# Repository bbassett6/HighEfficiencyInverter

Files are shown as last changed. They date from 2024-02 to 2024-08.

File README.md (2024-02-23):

Project Executive Summary

What is the design problem and why it should be solved?

With the growing popularity of student-led solar car racing competitions, newly established teams can have restrictive levels of funding to start their engineering endeavors. One of the most critical components of the competitiveness of their cars is the powertrain efficiency, which is heavily influenced by the quality and versatility of their motor controller. As of today, there are only two competitive options that are adopted by most teams, and both represent a substantial amount of the vehicle's cost (over a third of the electrical system's, approximately). This creates a tall barrier of entry for developing engineers to be exposed to real-life design environments that could deeply affect their career choices and subsequent impact in the world, which is why an open-source, accessible inverter would be impactful in the field of sustainable energy, and potentially many others.

What are the technical problems?

Technical problems include
•	Obtaining efficiency range values comparable or superior to present competitors’ while offering a substantially reduced price: 
Because of the size of the market, no substantial innovation has been made in mainstream options for approximately 14 years. Recent developments in SiC and GaN-based semiconductors could contribute a significant advantage compared to these outdated designs, but hitting required performance levels for a large range of possible motor and voltage configurations will be a challenge. Additionally, new control methodologies might be more applicable nowadays because of both device development and advances in control theory.
•	Maximizing efficiency while keeping the inverter design as tolerant as possible to high-voltage design changes depending on the application: 
Teams' choices of power per motor and DC bus voltage can vary drastically depending on the competition segment (multi- or single-occupant vehicles), creating a challenging optimization problem when attempting to make a product as efficient as possible for as many configurations as expected.
•	Minimizing inverter-driven high voltage system requirements: 
In addition to the DC bus compatibility, motor and motor sensing versatility is a factor that influences how seamless the product's integration can be, facilitating its adoption and potentially expanding its impact.
•	Power density (gravimetric, volumetric):
Being heavily influenced by the switching speed of the semiconductor devices being employed, recent product releases could be incredibly important to meet performance levels such as the DOE's 2025 Vehicle Technology goals.

What is the overall design/technical/objective(s)?

Design a financially (under US$ 1000) and technically accessible, high efficiency inverter for use in solar vehicle applications. The design should be easily replicable, testable, and employed by high-school level students. The final efficiency characteristics for applicable performance ranges (e.g. torque, speed, temperature), should be compatible with or surpass those of available options (WaveSculptor22, Mitsuba).

What is the proof of concept? What demonstrates that the solution works?

The proof of concept for the project could consist of a custom-made PCB for the selected power stage topology, containing components such as the switching devices, gate drivers, & high-voltage sensors. This would be complemented with an off-the-shelf development board containing the selected microcontroller and required peripherals, allowing full validation and operation of the converter without a finalized case and custom logic-stage PCB. Should this implementation work as expected, the project would move forward to unification and/or further customization of the boards to achieve a final unified package that is easily integrable.

Demonstrating the solution may involve attaching either an inductive load or a real motor to the inverter and measuring power losses through the power stage at various operating points (steady state cruising, acceleration, regenerative braking).

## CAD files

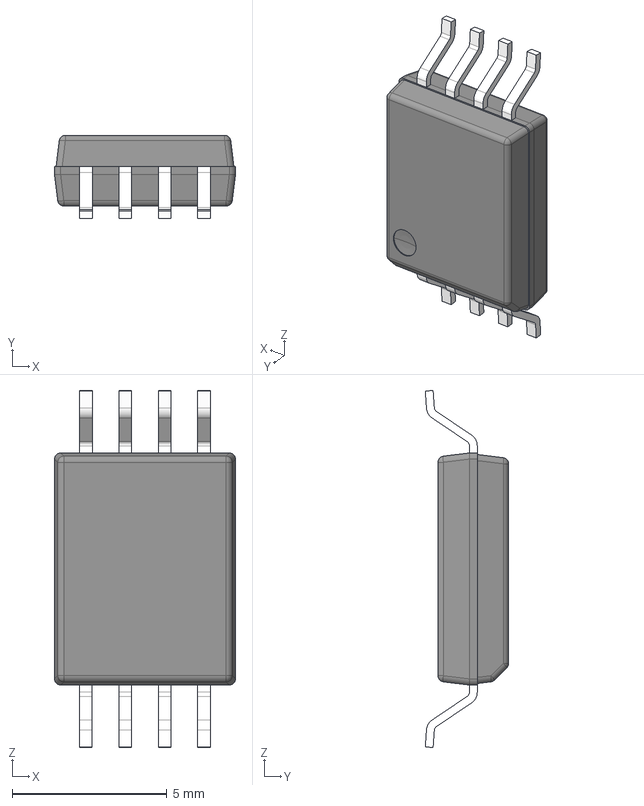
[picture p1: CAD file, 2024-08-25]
HEI_Power_Stage/Parts/AMC1311_KiCad/3D/AMC1311DWVR.stp
5.85 x 2.70 x 11.5 mm
BODY-SOIC
LEAD-DWV0008A x 8

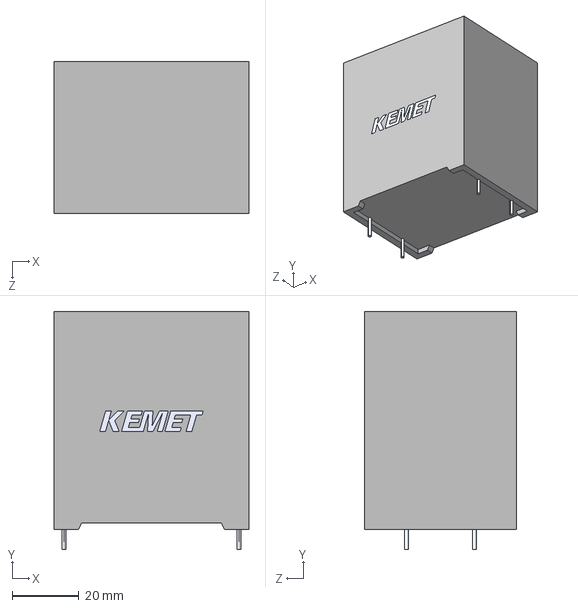
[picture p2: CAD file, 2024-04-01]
HEI_Power_Stage/Parts/C4AQ/C4AQLEW6210A3BK.stp
58.3 x 71.3 x 45.5 mm

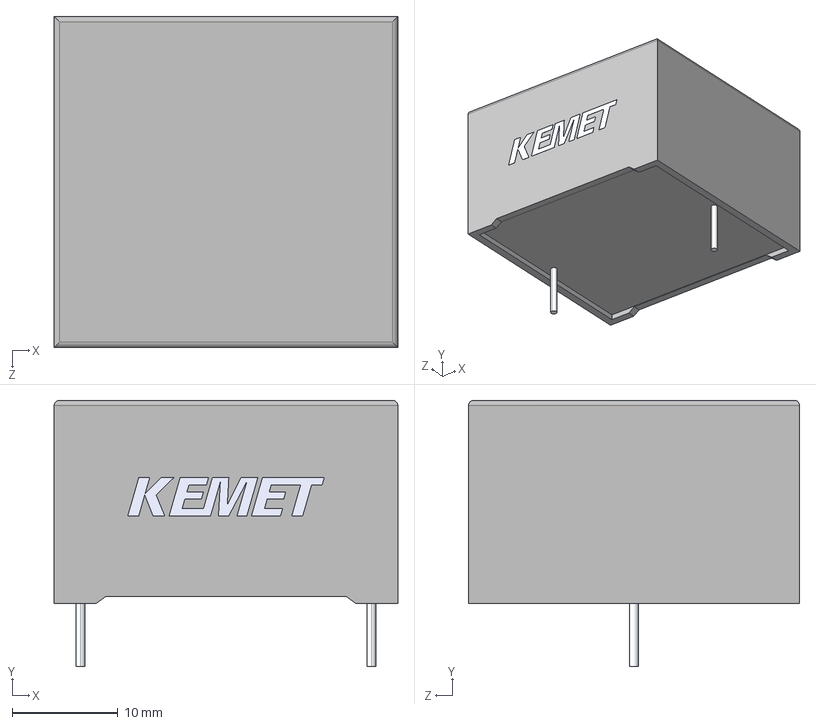
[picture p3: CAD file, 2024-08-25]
HEI_Power_Stage/Parts/C4AQLLU5150A19K _KiCad/3D/C4AQLLU5150A19K.stp
32.5 x 25.2 x 31.3 mm

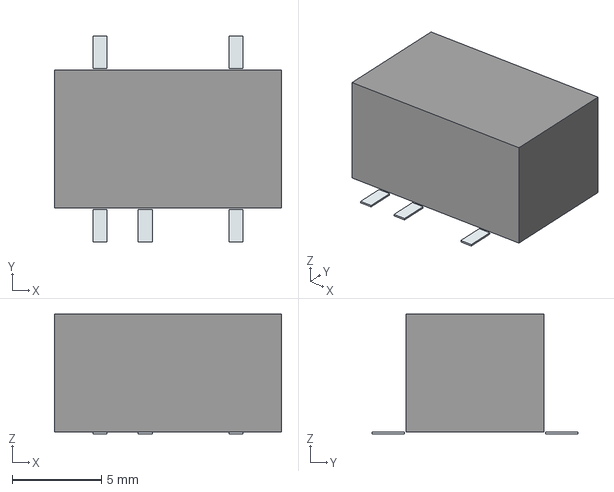
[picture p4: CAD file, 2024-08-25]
HEI_Power_Stage/Parts/CRE1S0505MC_KiCad/3D/CRE1S0505MC.stp
12.7 x 11.5 x 6.70 mm
Pins

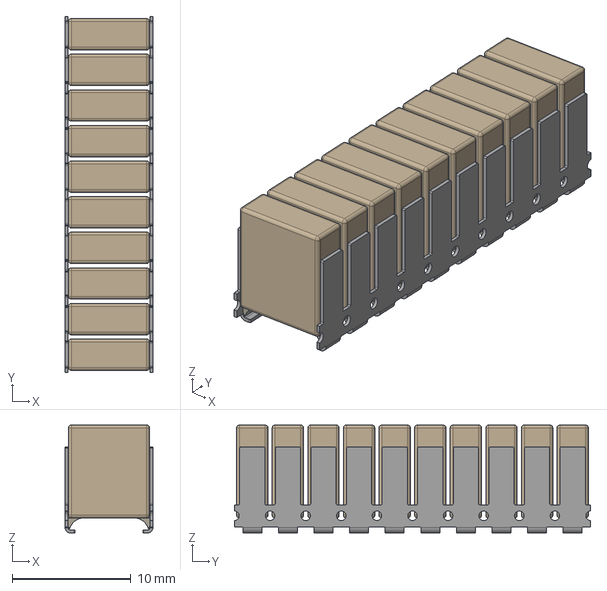
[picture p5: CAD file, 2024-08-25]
HEI_Power_Stage/Parts/B58035U5106M001_KiCad/3D/B58035U5106M001.stp
7.40 x 30.0 x 9.10 mm

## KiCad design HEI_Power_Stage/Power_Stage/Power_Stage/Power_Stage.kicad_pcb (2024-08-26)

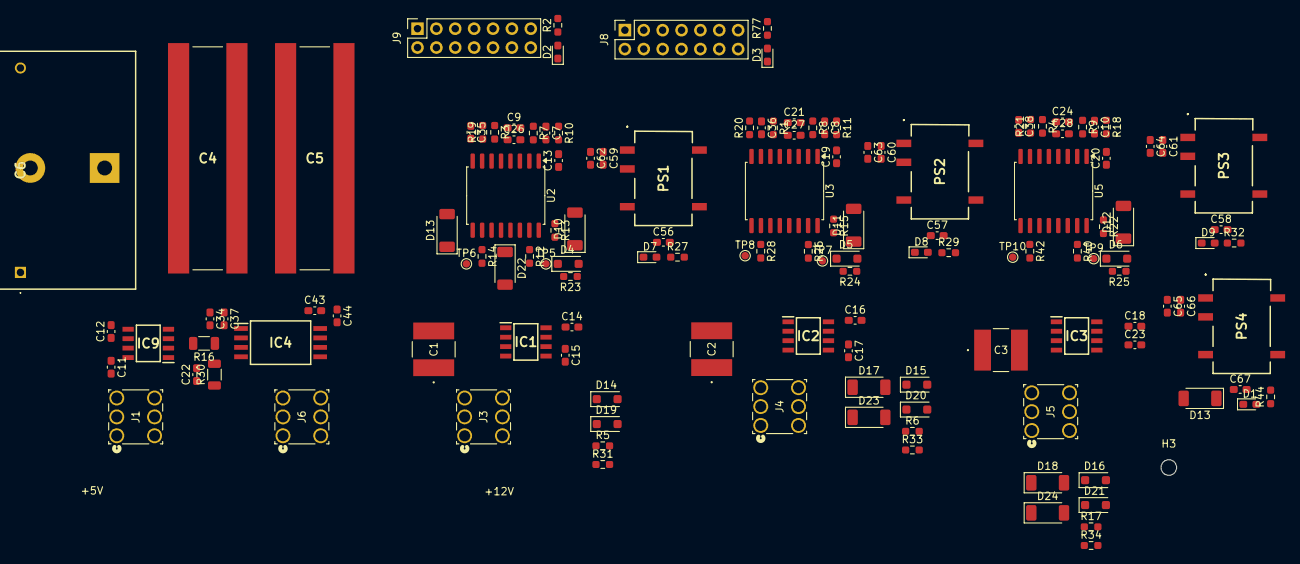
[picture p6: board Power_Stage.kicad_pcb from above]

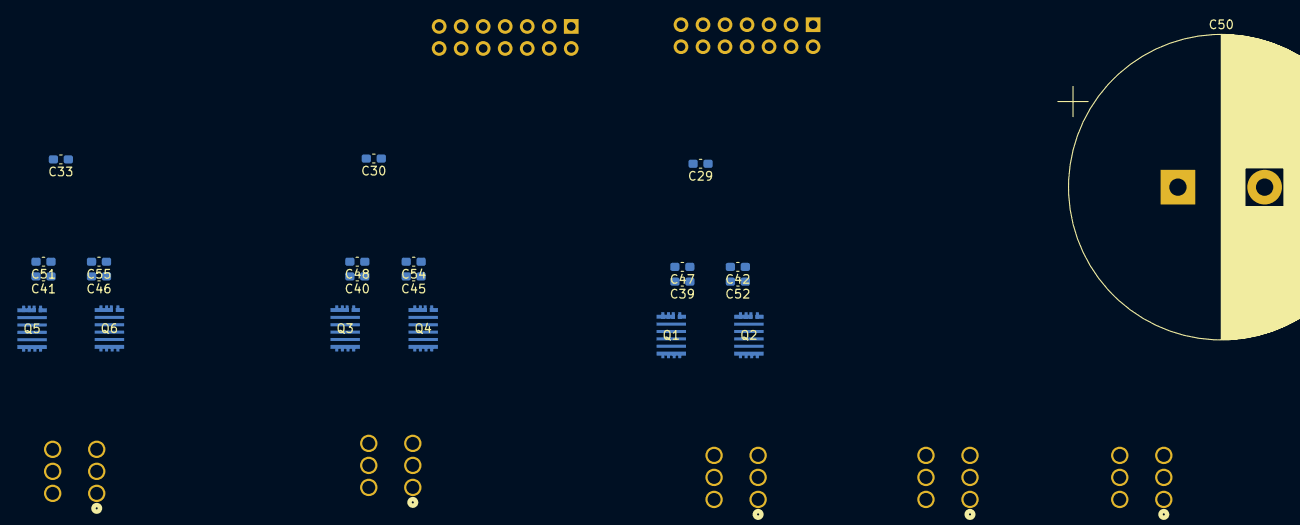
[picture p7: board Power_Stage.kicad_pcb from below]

Board: 4 copper layers, 160 parts (22 on the bottom side), 74 nets, no tracks yet.

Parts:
C1, C2, C3: 3.3uF; CAP_6050_TDK
C4, C5: B58035U5106M001
C6: 15uF; C4AQLLU5150A19K
C7, C8, C10, C13, C19, C20: 470pF; C_0603_1608Metric_Pad1.08x0.95mm_HandSolder
C9, C21, C24: 10uF; C_0603_1608Metric_Pad1.08x0.95mm_HandSolder
C11, C14, C16, C18, C29, C30, C33, C47, C48, C51, C52, C54, C55: 0.1uF; C_0603_1608Metric_Pad1.08x0.95mm_HandSolder
C12, C15, C17, C23: 1nF; C_0603_1608Metric_Pad1.08x0.95mm_HandSolder
C22: 10nF; C_0603_1608Metric_Pad1.08x0.95mm_HandSolder
C26, C27, C28, C34, C39, C40, C41, C42, C43, C45, C46, C59, C60, C61, C66: 1uF; C_0603_1608Metric_Pad1.08x0.95mm_HandSolder
C35, C36, C38: 2.2nF; C_0603_1608Metric_Pad1.08x0.95mm_HandSolder
C37, C44: 100nF; C_0603_1608Metric_Pad1.08x0.95mm_HandSolder
C50: 100uF; CP_Radial_D35.0mm_P10.00mm_SnapIn
C56, C57, C58, C62, C63, C64, C65, C67: 4.7uF; C_0603_1608Metric_Pad1.08x0.95mm_HandSolder
D1, D2, D3, D7, D8, D9: G; LED_0603_1608Metric_Pad1.05x0.95mm_HandSolder
D4, D5, D6, D14, D15, D16, D19, D20, D21: 300mV 1A; D_SOD-123F
D10, D11, D12, D13, D13#2, D17, D18, D22, D23, D24: PDZVTFTR5.1B; D_SOD-128
H1, H2, H3, H4: No. 8; MountingHole_2.1mm
IC1, IC2, IC3, IC9: ACS730KLCTR-65ABT; SOIC127P600X175-8N
IC4: AMC1311DWVR; SOIC127P1150X280-8N
J1, J3, J4, J5, J6: Screw_Terminal_01x01; CONN6_1057_WRE
J8, J9: Conn_02x07_Odd_Even; PinSocket_2x07_P2.54mm_Vertical
PS1, PS2, PS3, PS4: CRE1S0505MC
Q1, Q2, Q3, Q4, Q5, Q6: EPC2304ENGRT; EPC2304_ECC
R1, R3, R4, R5, R6, R7, R8, R9, R10, R11, R13, R15, R17, R18, R22, R23, R24, R25, R31, R33, R34: 0; R_0603_1608Metric_Pad0.98x0.95mm_HandSolder
R2, R27, R29, R32, R44: 440; R_0603_1608Metric_Pad0.98x0.95mm_HandSolder
R12, R14, R26, R28, R40, R42: 0.75; R_0603_1608Metric_Pad0.98x0.95mm_HandSolder
R16: 1Meg; R_1206_3216Metric
R19, R20, R21: 10k; R_0603_1608Metric_Pad0.98x0.95mm_HandSolder
R30: 10k; R_1206_3216Metric
R77: 1.2k; R_0603_1608Metric_Pad0.98x0.95mm_HandSolder
TP5, TP6, TP7, TP8, TP9, TP10: Test_Point; TestPoint_Pad_D1.0mm
U2, U3, U5: MP18831-4AGY; SOIC-16W_7.5x10.3mm_P1.27mm

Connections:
+5V_HV: C34.2, C37.2, C42.2, C45.2, C46.2, C52.2, C54.2, C55.2, C67.2, IC4.1 (VDD1), PS4.8 (+VOUT), R23.2, R24.2, R25.2, R44.2, U2.11 (VDDB), U3.11 (VDDB), U5.11 (VDDB)
+5V_LV: C9.2, C11.1, C14.1, C16.1, C18.1, C21.2, C24.2, C26.2, C27.2, C28.2, C29.2, C30.2, C33.2, C43.2, C44.2, C59.2, C60.2, C61.2, C62.2, C63.2, C64.2, C65.2, C66.2, IC1.8 (VCC), IC2.8 (VCC), IC3.8 (VCC), IC4.8 (VDD2), IC9.8 (VCC), J9.13, PS1.3 (+VIN), PS2.3 (+VIN), PS3.3 (+VIN), PS4.3 (+VIN), R1.1, R2.2, R3.1, R4.1, U2.3 (VDDI), U2.8 (VDDI), U3.3 (VDDI), U3.8 (VDDI), U5.3 (VDDI), U5.8 (VDDI)
+12V_LV: J8.13, R77.2
/AHS_{PWM}: J8.1, R10.1
/ALS_{PWM}: J8.3, R7.1
/BHS_{PWM}: J8.5, R11.1
/BLS_{PWM}: J8.7, R8.1
/CHS_{PWM}: J8.9, R18.1
/CLS_{PWM}: J8.11, R9.1
/DCI_{sense}ref: C12.1, IC9.6 (VZCR), J9.4
/DCV_{sense}M: IC4.6 (VOUTN), J9.6
/DCV_{sense}P: IC4.7 (VOUTP), J9.8
/PHA: IC1.3 (IP-_1), IC1.4 (IP-_2), J3.1, J3.2 (Pin_1), J3.3 (Pin_1), J3.4 (Pin_1), J3.5 (Pin_1), J3.6 (Pin_1)
/PHAI_{sense}: IC1.7 (VIOUT), J9.1
/PHAI_{sense}ref: C15.1, IC1.6 (VZCR), J9.3
/PHB: IC2.3 (IP-_1), IC2.4 (IP-_2), J4.1, J4.2 (Pin_1), J4.3 (Pin_1), J4.4 (Pin_1), J4.5 (Pin_1), J4.6 (Pin_1)
/PHBI_{sense}: IC2.7 (VIOUT), J9.5
/PHBI_{sense}ref: C17.1, IC2.6 (VZCR), J9.7, J9.11
/PHC: IC3.3 (IP-_1), IC3.4 (IP-_2), J5.1, J5.2 (Pin_1), J5.3 (Pin_1), J5.4 (Pin_1), J5.5 (Pin_1), J5.6 (Pin_1)
/PHCI_{sense}: IC3.7 (VIOUT), J9.9
/PHCI_{sense}ref: C23.1, IC3.6 (VZCR)
/Phase1/DT: C35.2, R19.1, U2.6 (DT)
/Phase1/EN: R3.2, U2.5 (EN)
/Phase1/HS_{DRV}: R5.1, R12.1, U2.15 (OUTA)
/Phase1/HS_{Gate}: D14.2 (A), D22.1 (K), Q1.1, R12.2, TP5.1
/Phase1/INA: C13.2, R10.2, U2.1 (INA)
/Phase1/INB: C7.2, R7.2, U2.2 (INB)
/Phase1/LS_{DRV}: R14.1, R31.1, U2.10 (OUTB)
/Phase1/LS_{Gate}: D13.1 (K), D13#2.1 (K), D19.2 (A), Q2.1, R14.2, TP6.1
/Phase1/SW: C39.1, C47.1, C56.1, D7.1 (K), D10.2 (A), D22.2 (A), IC1.1 (IP+_1), IC1.2 (IP+_2), PS1.7 (-VOUT), Q1.2, Q1.4, Q1.6, Q2.3, Q2.5, Q2.7, U2.14 (VSSA)
/Phase1/VDDA: C56.2, D10.1 (K), PS1.8 (+VOUT), R13.1, R27.2
/Phase1/VDDhs: C39.2, C47.2, D4.1 (K), R13.2, U2.16 (VDDA)
/Phase2/DT: C36.2, R20.1, U3.6 (DT)
/Phase2/EN: R1.2, U3.5 (EN)
/Phase2/HS_{DRV}: R6.1, R26.1, U3.15 (OUTA)
/Phase2/HS_{Gate}: D15.2 (A), D23.1 (K), Q3.1, R26.2, TP7.1
/Phase2/INA: C19.2, R11.2, U3.1 (INA)
/Phase2/INB: C8.2, R8.2, U3.2 (INB)
/Phase2/LS_{DRV}: R28.1, R33.1, U3.10 (OUTB)
/Phase2/LS_{Gate}: D17.1 (K), D20.2 (A), Q4.1, R28.2, TP8.1
/Phase2/SW: C40.1, C48.1, C57.1, D8.1 (K), D11.2 (A), D23.2 (A), IC2.1 (IP+_1), IC2.2 (IP+_2), PS2.7 (-VOUT), Q3.2, Q3.4, Q3.6, Q4.3, Q4.5, Q4.7, U3.14 (VSSA)
/Phase2/VDDA: C57.2, D11.1 (K), PS2.8 (+VOUT), R15.1, R29.2
/Phase2/VDDhs: C40.2, C48.2, D5.1 (K), R15.2, U3.16 (VDDA)
/Phase3/DT: C38.2, R21.1, U5.6 (DT)
/Phase3/EN: R4.2, U5.5 (EN)
/Phase3/HS_{DRV}: R17.1, R40.1, U5.15 (OUTA)
/Phase3/HS_{Gate}: D16.2 (A), D24.1 (K), Q5.1, R40.2, TP9.1
/Phase3/INA: C20.2, R18.2, U5.1 (INA)
/Phase3/INB: C10.2, R9.2, U5.2 (INB)
/Phase3/LS_{DRV}: R34.1, R42.1, U5.10 (OUTB)
/Phase3/LS_{Gate}: D18.1 (K), D21.2 (A), Q6.1, R42.2, TP10.1
/Phase3/SW: C41.1, C51.1, C58.1, D9.1 (K), D12.2 (A), D24.2 (A), IC3.1 (IP+_1), IC3.2 (IP+_2), PS3.7 (-VOUT), Q5.2, Q5.4, Q5.6, Q6.3, Q6.5, Q6.7, U5.14 (VSSA)
/Phase3/VDDA: C58.2, D12.1 (K), PS3.8 (+VOUT), R22.1, R32.2
/Phase3/VDDhs: C41.2, C51.2, D6.1 (K), R22.2, U5.16 (VDDA)
GND: C7.1, C8.1, C9.1, C10.1, C11.2, C12.2, C13.1, C14.2, C15.2, C16.2, C17.2, C18.2, C19.1, C20.1, C21.1, C23.2, C24.1, C26.1, C27.1, C28.1, C29.1, C30.1, C33.1, C35.1, C36.1, C38.1, C43.1, C44.1, C59.1, C60.1, C61.1, C62.1, C63.1, C64.1, C65.1, C66.1, D2.1 (K), D3.1 (K), IC1.5 (GND), IC2.5 (GND), IC3.5 (GND), IC4.5 (GND2), IC9.5 (GND), J8.14, J9.14, PS1.1 (-VIN), PS2.1 (-VIN), PS3.1 (-VIN), PS4.1 (-VIN), R19.2, R20.2, R21.2, U2.4 (GNDI), U3.4 (GNDI), U5.4 (GNDI)
HV+: C1.1, C2.1, C3.1, C4.2, C5.2, C6.2, C50.1, IC9.3 (IP-_1), IC9.4 (IP-_2), Q1.3, Q1.5, Q1.7, Q3.3, Q3.5, Q3.7, Q5.3, Q5.5, Q5.7, R16.2
HV+in: IC9.1 (IP+_1), IC9.2 (IP+_2), J1.1, J1.2 (Pin_1), J1.3 (Pin_1), J1.4 (Pin_1), J1.5 (Pin_1), J1.6 (Pin_1)
HV-: C1.2, C2.2, C3.2, C4.1, C5.1, C6.1, C22.1, C34.1, C37.1, C42.1, C45.1, C46.1, C50.2, C52.1, C54.1, C55.1, C67.1, D1.1 (K), D13.2 (A), D13#2.2 (A), D17.2 (A), D18.2 (A), IC4.3 (SHTDN), IC4.4 (GND1), J6.1, J6.2 (Pin_1), J6.3 (Pin_1), J6.4 (Pin_1), J6.5 (Pin_1), J6.6 (Pin_1), PS4.7 (-VOUT), Q2.2, Q2.4, Q2.6, Q4.2, Q4.4, Q4.6, Q6.2, Q6.4, Q6.6, R30.1, U2.9 (VSSB), U3.9 (VSSB), U5.9 (VSSB)
unnamed: D1.2 (A), R44.1
unnamed: D2.2 (A), R2.1
unnamed: D3.2 (A), R77.1
unnamed: D4.2 (A), R23.1
unnamed: D5.2 (A), R24.1
unnamed: D6.2 (A), R25.1
unnamed: D7.2 (A), R27.1
unnamed: D8.2 (A), R29.1
unnamed: D9.2 (A), R32.1
unnamed: D14.1 (K), R5.2
unnamed: D15.1 (K), R6.2
unnamed: D16.1 (K), R17.2
unnamed: D19.1 (K), R31.2
unnamed: D20.1 (K), R33.2
unnamed: D21.1 (K), R34.2
unnamed: C22.2, IC4.2 (VIN), R16.1, R30.2

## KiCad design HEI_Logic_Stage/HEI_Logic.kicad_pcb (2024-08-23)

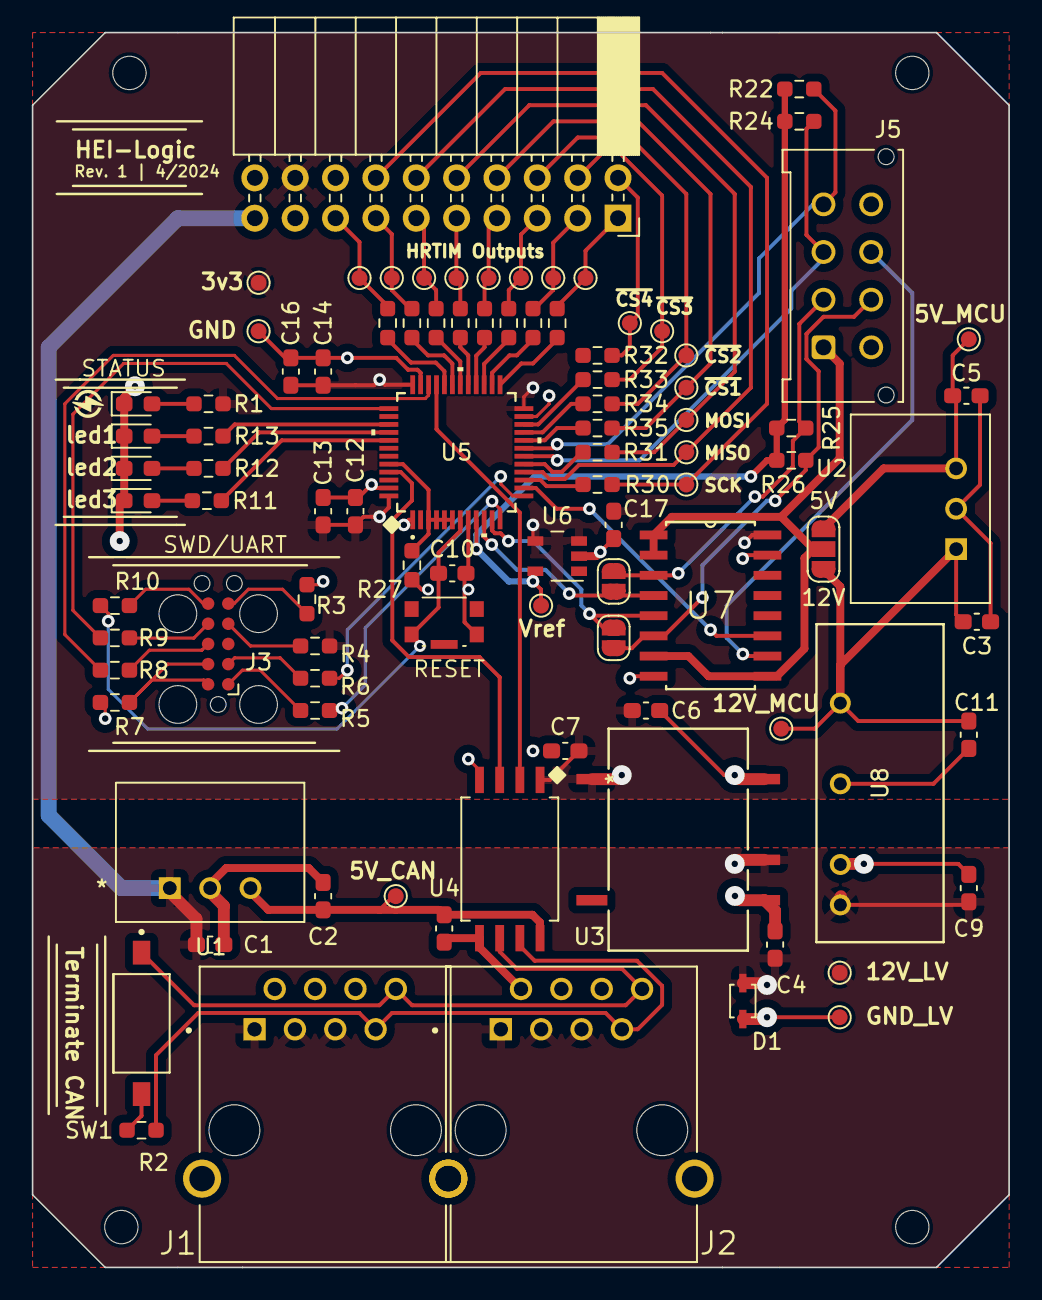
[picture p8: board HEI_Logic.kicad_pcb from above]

Board: 4 copper layers, 61.5 x 77.7 mm, 98 parts (0 on the bottom side), 72 nets.

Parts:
C1, C2, C3, C5, C6: 10uF; C_0603_1608Metric_Pad1.08x0.95mm_HandSolder
C4: 2.2uF; C_0603_1608Metric_Pad1.08x0.95mm_HandSolder
C7, C8, C10, C12, C13, C14, C17: 0.1uF; C_0603_1608Metric_Pad1.08x0.95mm_HandSolder
C9, C11: 1uF; C_0603_1608Metric_Pad1.08x0.95mm_HandSolder
C16: 4.7uF; C_0603_1608Metric_Pad1.08x0.95mm_HandSolder
D1: 12V_TVS_ESD12VD3B-TP; ESD12VD3B-TP
D2: LED_Green; LED_0603_1608Metric_Pad1.05x0.95mm_HandSolder
D3, D4, D5: LED_Orange; LED_0603_1608Metric_Pad1.05x0.95mm_HandSolder
H1, H2, H3, H4: No. 8; MountingHole_2.1mm
J1: RJ_{1}; ASSMANN_A-2004-2-4-LPS-N-R
J2: RJ_{2}; ASSMANN_A-2004-2-4-LPS-N-R
J3: Tag-Connect; Tag-Connect_TC2050-IDC-FP_2x05_P1.27mm_Vertical
J4: Conn_02x10_Odd_Even; PinSocket_2x10_P2.54mm_Horizontal
J5: 430450813_Molex; Molex_Micro-Fit_3.0_43045-0812_2x04_P3.00mm_Vertical
JP1: Jumper_3_Open; SolderJumper-3_P1.3mm_Open_RoundedPad1.0x1.5mm_NumberLabels
JP4, JP5: Jumper_2_Open; SolderJumper-2_P1.3mm_Open_RoundedPad1.0x1.5mm
R1: 100; R_0603_1608Metric_Pad0.98x0.95mm_HandSolder
R2: 120; R_0603_1608Metric_Pad0.98x0.95mm_HandSolder
R3, R4, R5, R6, R7, R8, R9, R10: 150; R_0603_1608Metric_Pad0.98x0.95mm_HandSolder
R11, R12, R13: 220; R_0603_1608Metric_Pad0.98x0.95mm_HandSolder
R14, R15, R16, R17, R18, R19, R20, R21, R30, R31, R32, R33, R34, R35: 330; R_0603_1608Metric_Pad0.98x0.95mm_HandSolder
R22, R24, R25, R26: X; R_0603_1608Metric_Pad0.98x0.95mm_HandSolder
R27: 10k; R_0603_1608Metric_Pad0.98x0.95mm_HandSolder
SW1: SW_SPST; SW_DS04-254-1-01BK-SMT
SW2: SW_Push; KMR223GLFG
TP1, TP2, TP3, TP4, TP5, TP6, TP7, TP8, TP9, TP10, TP11, TP12, TP13, TP14, TP15, TP16, TP17, TP18, TP19, TP20, TP21, TP22, TP23: Test_Point; TestPoint_Pad_D1.0mm
U1, U2: 5V_Converter_R-78E5.0-0.5; R-78E5.0-0.5
U3: B1203XT-1WR3; B_XT-1WR3_MNS-M
U4: ADM3058EBRIZ; 8-SOIC_ADM3058EBRIZ
U5: STM32F334C8T6; LQFP48-7x7mm
U6: LM4132-Q1 SOT-2; 3V_Ref_LM4132AQ1MFT3.0_SOT235
U7: CD40109BQNSRQ1; SOIC127P780X200-16N
U8: TMH 1212S; TMH SINGLE_TRP

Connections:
+3V3: C6.1, C7.2, C12.2, C13.2, C14.2, C16.1, C17.1, J4.18, R1.2, R4.1, TP10.1, U3.5 (+VO), U4.1 (VDD1), U5.1 (VBAT), U5.24 (VDD_1), U5.36 (VDDUSB), U5.48 (VDD_2), U6.3 (EN), U6.4 (VIN), U7.16 (VDD)
/5V_CAN: C2.1, C8.2, TP9.1, U1.3 (+VOUT), U4.8 (VDD2)
/5V_MCU: C5.1, JP1.1 (A), TP22.1, U2.3 (+VOUT)
/10kSaver: R27.2, U5.3 (PC14-OSC32_IN), U5.4 (PC15-OSC32_OUT), U5.5 (PH0-OSC_IN), U5.6 (PH1-OSC_OUT), U5.44 (PH3-BOOT0)
/12V_LV: C1.1, C4.1, C9.1, D1.2, J1.1, J1.3, J1.5, J2.1, J2.3, J2.5, J4.19, TP14.1, U1.1 (+VIN), U3.2 (VIN), U8.1 (+VIN(VCC))
/12V_MCU: C3.1, C11.1, JP1.3 (B), TP23.1, U2.1 (+VIN), U8.6 (+VOUT)
/CANH: J1.7, J2.7, R2.1, U4.7 (CANH)
/CANL: J1.8, J2.8, SW1.1 (A), U4.6 (CANL)
/CAN_RX: U4.3 (RXD), U5.45 (PB8)
/CAN_TX: U4.2 (TXD), U5.33 (PA12)
/GND_LV: C1.2, C2.2, C4.2, C8.1, C9.2, D1.1, J1.2, J1.4, J1.6, J1.S1, J1.S2, J2.2, J2.4, J2.6, J4.20, TP13.1, U1.2 (GND), U3.1 (GND), U4.5 (GND2), U8.2 (-VIN(GND))
/HRTIM_A1: J4.9, R18.1, TP5.1
/HRTIM_A1_r: R18.2, U5.29 (PA8)
/HRTIM_A2: J4.11, R17.1, TP6.1
/HRTIM_A2_r: R17.2, U5.30 (PA9)
/HRTIM_B1: J4.13, R19.1, TP7.1
/HRTIM_B1_r: R19.2, U5.31 (PA10)
/HRTIM_B2: J4.15, R20.1, TP8.1
/HRTIM_B2_r: R20.2, U5.32 (PA11)
/HRTIM_C1: J4.1, R14.2, TP1.1
/HRTIM_C1_r: R14.1, U5.25 (PB12)
/HRTIM_C2: J4.3, R15.2, TP2.1
/HRTIM_C2_r: R15.1, U5.26 (PB13)
/HRTIM_D1: J4.5, R16.2, TP3.1
/HRTIM_D1_r: R16.1, U5.27 (PB14)
/HRTIM_D2: J4.7, R21.2, TP4.1
/HRTIM_D2_r: R21.1, U5.28 (PB15)
/HallIN1_3v3/ADC: JP4.1 (A), U5.10 (PA0), U7.4 (E)
/HallIN1/TIN3: J5.2, JP4.2 (B), R25.2, U7.3 (A)
/HallIN2_3v3/ADC: JP5.1 (A), U5.11 (PA1), U7.5 (F)
/HallIN2/TIN4: J5.6, JP5.2 (B), R26.2, U7.6 (B)
/HallIN3: J5.7, U7.10 (C)
/HallIN3_3v3: U5.14 (PA4), U7.11 (G)
/LED1: R13.2, U5.39 (PB3)
/LED2: R12.2, U5.40 (PB4)
/LED3: R11.2, U5.41 (PB5)
/MISO: J4.12, TP20.1, U5.16 (PA6)
/MOSI: J4.10, R31.1, TP21.1
/MOSI_r: R31.2, U5.17 (PA7)
/SCK: J4.14, R30.1, TP19.1
/SCK_r: R30.2, U5.15 (PA5)
/SWDCLK: R9.1, U5.37 (PA14)
/SWDIO: R8.1, U5.34 (PA13)
/TIN1: J5.3, R24.2, U5.18 (PB0)
/TIN2: J5.4, R22.2, U5.19 (PB1)
/UART_RX: R6.1, U5.13 (PA3)
/UART_TX: R5.2, U5.12 (PA2)
/V_Hall: J5.1, JP1.2 (C), U7.1 (VCC), U7.2 (EN_A), U7.7 (EN_B), U7.9 (EN_C)
/Vref: R22.1, R24.1, R25.1, R26.1, TP11.1, U5.9 (VDDA/VREF_P), U6.5 (VREF)
/~CS1: J4.8, R35.1, TP16.1
/~CS1_r: R35.2, U5.20 (PB2)
/~CS2: J4.6, R34.1, TP17.1
/~CS2_r: R34.2, U5.21 (PB10)
/~CS3: J4.4, R33.1, TP18.1
/~CS3_r: R33.2, U5.22 (PB11)
/~CS4: J4.2, R32.1, TP15.1
/~CS4_r: R32.2, U5.38 (PA15)
/~RST: C10.1, R10.1, SW2.2, U5.7 (~RST)
GND: C3.2, C5.2, C6.2, C7.1, C10.2, C11.2, C12.1, C13.1, C14.1, C16.2, C17.2, D2.1 (K), D3.1 (K), D4.1 (K), D5.1 (K), J4.16, J4.17, J5.5, J5.8, R3.1, R7.1, R27.1, SW2.1, TP12.1, U2.2 (GND), U3.4 (0V), U4.4 (GND1), U5.8 (VSSA/VREF_M), U5.23 (VSS_1), U5.35 (VSS_2), U5.47 (VSS_3), U6.2 (GND), U7.8 (VSS), U7.15 (EN_D), U8.4 (-VOUT)
unnamed: D2.2 (A), R1.1
unnamed: D3.2 (A), R11.1
unnamed: D4.2 (A), R12.1
unnamed: D5.2 (A), R13.1
unnamed: J3.1, R5.1
unnamed: J3.2, R6.2
unnamed: J3.4, R4.2
unnamed: J3.5, R3.2
unnamed: J3.6, R10.2
unnamed: J3.7, R9.2
unnamed: J3.8, R8.2
unnamed: J3.9, J3.10, R7.2
unnamed: R2.2, SW1.2 (B)

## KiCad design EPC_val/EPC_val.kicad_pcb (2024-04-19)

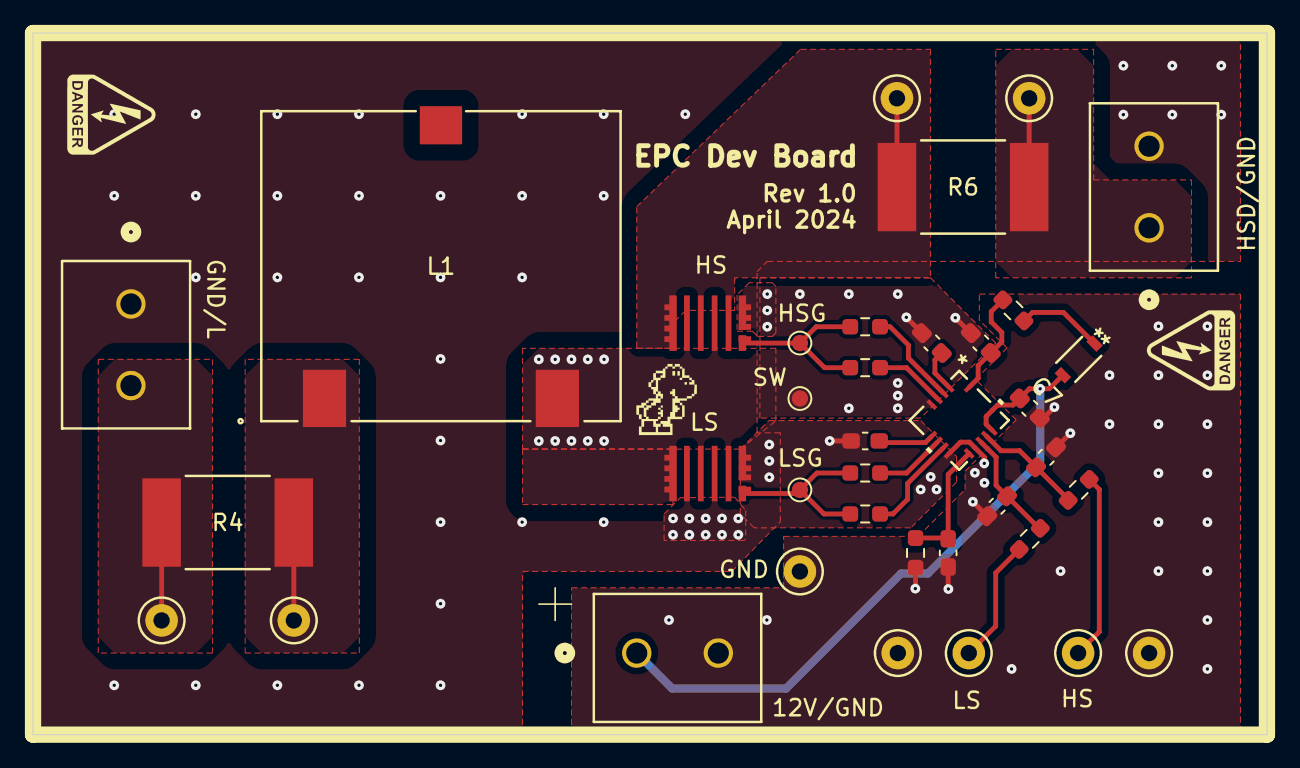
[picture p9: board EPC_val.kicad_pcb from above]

Board: 4 copper layers, 75.6 x 43.0 mm, 37 parts (0 on the bottom side), 22 nets.

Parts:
12V/GND: 691137710002; CONN2_710002_WRE
C1, C2: 15pF; C_0603_1608Metric_Pad1.08x0.95mm_HandSolder
C3: 0.1uF; C_0603_1608Metric_Pad1.08x0.95mm_HandSolder
C4, C5, C7: 1uF; C_0603_1608Metric_Pad1.08x0.95mm_HandSolder
C6: 470nF; C_0603_1608Metric_Pad1.08x0.95mm_HandSolder
D1: RFU02VSM6STR; DIO_RFU02VS_ROM-M
GND: Test_Point; TestPoint_Keystone_5000-5004_Miniature
GND#2, GND#3: Test_Point; TestPoint_Keystone_5000-5004_Miniature
GND/L: 691137710002; CONN2_710002_WRE
HS: EPC2304ENGRT; EPC2304_ECC
HS#2: Test_Point; TestPoint_Keystone_5000-5004_Miniature
HSD/GND: 691137710002; CONN2_710002_WRE
HSG: Test_Point; TestPoint_Pad_D1.0mm
L1: 58 uH; IND_6000A_MUR
LS: EPC2304ENGRT; EPC2304_ECC
LS#2: Test_Point; TestPoint_Keystone_5000-5004_Miniature
LSG: Test_Point; TestPoint_Pad_D1.0mm
R1, R2: 2.2 0.1W; R_0603_1608Metric_Pad0.98x0.95mm_HandSolder
R3: 50k; R_0603_1608Metric_Pad0.98x0.95mm_HandSolder
R4, R6: PU3921FKM130U5L; RES_PU3921_.5mOHM_YAG-L
R5: 2 1/16W; R_0603_1608Metric_Pad0.98x0.95mm_HandSolder
R7, R9: 0.47 1/16W; R_0603_1608Metric_Pad0.98x0.95mm_HandSolder
R8, R10: 0 1/16W; R_0603_1608Metric_Pad0.98x0.95mm_HandSolder
SW: Test_Point; TestPoint_Pad_D1.0mm
TP5, TP6, TP7, TP8: Test_Point; TestPoint_Keystone_5000-5004_Miniature
U1: NCP51820AMNTWG; QFN_0AMNTWG_ONS-L

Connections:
+12V: 12V/GND.1, C7.1, D1.2 (A), U1.13 (EN), U1.14 (VDD)
/DT: C3.2, R3.2, U1.9 (DT)
/HIN: C1.1, R1.1, U1.12 (HIN)
/HSD: HS.3, HS.5, HS.7, R6.1, TP7.1
/HS_{Gate}: HS.1, HSG.1, R7.2, R8.2
/HS_{PWM}: HS#2.1, R1.2
/HS_{SNK}: R8.1, U1.3 (HOSNK)
/HS_{SRC}: R7.1, U1.2 (HOSRC)
/In_HSD: HSD/GND.1, R6.2, TP8.1
/In_L: GND/L.2, R4.1, TP5.1
/L: L1.1, R4.2, TP6.1
/LIN: C2.1, R2.1, U1.11 (LIN)
/LS_{Gate}: LS.1, LSG.1, R9.2, R10.2
/LS_{PWM}: LS#2.1, R2.2
/LS_{SNK}: R10.1, U1.7 (LSONK)
/LS_{SRC}: R9.1, U1.6 (LOSRC)
/SW: C4.2, C6.2, HS.2, HS.4, HS.6, L1.2, LS.3, LS.5, LS.7, SW.1, U1.4 (SW)
/VDDH: C4.1, U1.1 (VDDH)
/VDDL: C5.2, U1.5 (VDDL)
/V_{BST}: C6.1, R5.2, U1.15 (VBST)
GND: 12V/GND.2, C1.2, C2.2, C3.1, C5.1, C7.2, GND.1, GND#2.1, GND#3.1, GND/L.1, HSD/GND.2, LS.2, LS.4, LS.6, R3.1, U1.8 (PGND), U1.10 (SGND)
unnamed: D1.1 (K), R5.1

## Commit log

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2024-03-14 Basic schematic outline
    schematic files to start
    [Connections.SchDoc, Gate Driver.SchDoc, HEI_Power_Stage.PrjPcb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]
2024-03-14 added epc gan fets library file
    stil trying to figure out how to have fully integrated database libraries because it will likely have a mix of custom and downloaded components
    [HEI_Power_Stage.SCHLIB, Mosfets.SchDoc]
2024-03-15 gate driver model
    gate driver added
    [HEI_Power_Stage.PrjPcb, NCP51820AMNTWG.PcbLib, NCP51820AMNTWG.SchLib]
2024-03-15 added current sense IC library
    TMCS1123
    pin compatible with tmcs1133, higher bandwidth but not in production, can try to ask ti for samples if 250 kHz is not enough
    [NCP51820AMNTWG.PcbLib, NCP51820AMNTWG.SchLib, TMCS1123A1AQDVGR.PcbLib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]
2024-03-15 saved all documents
    [Gate Driver.SchDoc, HEI_Power_Stage.PrjPcb, Mosfets.SchDoc]
2024-03-15 removed all altium files from HEI repo
    removed all altium files to use repo as the Kicad repo
    [Connections.SchDoc, Gate Driver.SchDoc, HEI_Power_Stage.PrjPcb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]
2024-03-15 kicad project
    [Power_Stage.kicad_pcb, Power_Stage.kicad_sch]
2024-03-16 added TMCS1123A1A
    added library for the tmcs1123 current sense
    [Power_Stage.kicad_sch]
2024-03-16 added libraries
    [Power_Stage.kicad_pcb, Power_Stage.kicad_sch]
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2024-03-18 second try for kicad libs
    [Power_Stage.kicad_pcb, Power_Stage.kicad_sch]
2024-03-24 preliminary schematic and layout for POC
    [Phase.kicad_sch, Power_Stage.kicad_pcb, Power_Stage.kicad_sch]
2024-03-25 initial phase a routing
    routed connections for phase A not including SPI. spi left as stubs that can be routed to connector and to the other ADCs.
    Power and PWRGND routing is done on layer 1,2,4 and can be discussed further in persons. For now I have VDC on layer 1 and 4. PWRGND on layer 1 and 4. SW and PHA on layer 1 and 2. layer 3 and 5 are g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
    [Phase.kicad_sch, Power_Stage.kicad_pcb, Power_Stage.kicad_sch]
2024-03-27 SPI and ldo
    wired spi and ldo, thinking about stackup layer assignments for power. Layer 4 could be all VDC and PWD GND only, routing VDC on the top half and PWRGND on the bottom half. Then layer 1,2 can be for 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
    [Power_Stage.kicad_pcb]
2024-03-27 changes in meeting
    [Power_Stage.kicad_pcb, Power_Stage.kicad_sch]
2024-03-27 added 12-12 footprint
    [Power_Stage.kicad_pcb]
2024-03-29 layout
    5v regulators for each phase daq
    12v iso
    top half and bottom half planes
    SPi goes from bottom to top layer at plane split
    power routed on bottom two layers with solid planes
    switch nodes on top two layers
    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
    [Phase.kicad_sch, Power_Stage.kicad_pcb, Power_Stage.kicad_sch]
2024-03-31 changes since class on friday
    solid gndpwr plane on layer 3
    new cap... its large
    [Phase.kicad_sch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]
2024-04-01 POC layout changes fro meeting
    Two cap options on the bottom:
    large kemet that would meet all requirements on its own
    also large cylindrical aluminum electrolytic that only has 4.3A riplpe current rating. can use either for testing. can also add more holes for trying other caps
    layer 3 now continous gndpwr for whole board.
    [C4AQLEW6210A3BK.stp, Phase.kicad_sch, Power_Stage.kicad_pcb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]
2024-04-01 silkscreen updates
    silkscreen should be all good
    drc silkscreen errors somewhat resolved
    added labels for TPs and LEDs
    added more stitching for top layer "gnd" on top half tor PWM ref
    holes all alligned
    [Power_Stage.kicad_pcb]
2024-04-03 small changes
    [Power_Stage.kicad_pcb]
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2024-04-05 added low pass filters, PGND/SGND jumper
    [LPF.kicad_sch, Phase.kicad_sch, Power_Stage.kicad_pcb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]
2024-04-10 spi isolation
    [LPF.kicad_sch, Phase.kicad_sch, Power_Stage.kicad_pcb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]
2024-04-10 more isolation
    [Power_Stage.kicad_sch, isolation.kicad_sch]
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2024-04-12 need to fix vias
    [EPC_val.kicad_pcb]
2024-04-12 git ignore pls work
    [Power_Stage.kicad_pcb]
2024-04-19 epc board should be ready to order
    [EPC_val.kicad_pcb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]
2024-04-19 added updated logic stage
    [HEI_Logic.kicad_pcb, HEI_Logic.kicad_sch]
2024-04-19 logic stage motor interface schematic
    [HEI_Logic.kicad_sch]
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2024-08-21 new gate driver
    added new gate drivers, changes sensing to be non isolated, removed adcs on gate drive pages, added connector, added dc link cap, need to still change isolation page to just be iso amp, need to adjus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
    [LPF.kicad_sch, isolation.kicad_sch]
2024-08-21 new power stage schematic
    added iso amp for hv bus sensing
    updated connectors
    removed isolation page
    added notes for new components
    need to decide if ADCs go on power or logic board for noise immunity or simpler power stage
    [Phase.kicad_sch, Power_Stage.kicad_sch]
2024-08-22 added second option for isolated amplifier
    added adum4195 and idolated dcdc
    new iso amp is single ended output so we can use regular single ended input ADC
    [Power_Stage.kicad_sch]
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2024-08-23 initial edits to logic stage schematic
    [HEI_Logic.kicad_pcb, HEI_Logic.kicad_sch]
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2024-08-25 I think all schematic done
    added new mps gate driver, new acs current sense, new differential voltage sense, new 5-5 iso converters.
    beginning layout
    [Isolated5V.kicad_sch, Phase.kicad_sch, Power_Stage.kicad_pcb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]
2024-08-25 more progress
    started placement for each half bridge
    3d bodies
    connectors sorted
    options for dc link cap
    [AMC1311DWVR.stp, B58035U5106M001.stp, C4AQLLU5150A19K.stp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]
2024-08-26 placement rough draft
    roughly placed all components
    [Phase.kicad_sch, Power_Stage.kicad_pcb, Power_Stage.kicad_sch]
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

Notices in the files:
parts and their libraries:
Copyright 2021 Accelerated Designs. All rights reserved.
